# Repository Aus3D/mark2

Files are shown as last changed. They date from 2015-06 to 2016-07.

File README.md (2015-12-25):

# Aus3D Mark2 3D Printer Kit

## Overview
The Aus3D Mark2 3D Printer kit is designed to be a high-quality, easy to assemble kit-based printer. Quality and capability were the primary design goals, and the Mark2 is a printer that will not disappoint in these areas. It is based off of the [RepRap Prusa Mendel i3](http://www.reprap.org/wiki/I3) design, however the Mark2 has been redesigned from the ground up to be sturdier and more capable than traditional i3-based printers. Threaded rod and printed fasteners have been replaced with extra-thick 10mm acrylic, and the frame has been designed to to reduce vibrations - minimising excess noise and improving print quality, even during strenuous, high-frequency motions. The typical threaded-rod Z-axis has been replaced with an improved lead screw driven system, reducing Z-backlash and allowing for smoother Z motion. The rigid frame ensures all axes are held square, ensuring optimal print quality.

Full details are available on the [Aus3D wiki](http://wiki.aus3d.com.au/Mark2_Documentation).

## License
<br /><span xmlns:dct="http://purl.org/dc/terms/" property="dct:title">MK2 Printer Kit</span> by <a xmlns:cc="http://creativecommons.org/ns#" href="http://www.aus3d.com.au" property="cc:attributionName" rel="cc:attributionURL">Aus3D</a> is licensed under a <a rel="license" href="http://creativecommons.org/licenses/by-nc-sa/4.0/">Creative Commons Attribution-NonCommercial-ShareAlike 4.0 International License</a>.

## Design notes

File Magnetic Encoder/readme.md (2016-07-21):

# Magnetic Encoder Mounting Parts

The parts in this folder can be printed and used to mount magnetic encoder modules and magnetic strips to the Mark2 printer.

## X Axis
### Required Parts
* 2 x 'x-strip-bracket'
* 1 x 'x-carriage-mount'
* 2 x M3 x 15mm bolts (replace 10mm bolts in X carriage)
* 2 x M3 x 20mm bolts (for mounting strip)
* 2 x M3 nuts (for mounting strip)
* 2 x springs (for mounting strip)

Additionally, one length of wood / plastic / metal roughly 310-360mm long x 10 - 50mm wide x 1 - 5mm thick is required, and two 3mm holes must be drilled through it spaced 297mm apart. This length of material is used for mounting the magnetic strip.

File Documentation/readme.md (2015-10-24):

Assembly instructions, and other up to date documentation, can be found on the Aus3D Wiki [here](http://wiki.aus3d.com.au/Mark2_Documentation)

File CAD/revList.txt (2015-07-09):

Z rod spacing changed to 22mm
Z bracket updated to attach via 2 screws (trialled on recent kits)
frame-side-panel screwhole cutouts all changed to 3.2mm for better fit
frame-side-panel tab-cutouts all changed to 8.4 x 8.4mm for better fit

All frame t-slots designed for M3 screws and M3 nyloc nuts
All frame t-slots have filleted edges to resist over-tightening
Standard screw lengths of 12mm and 18mm

Countersunk screws for heated bed

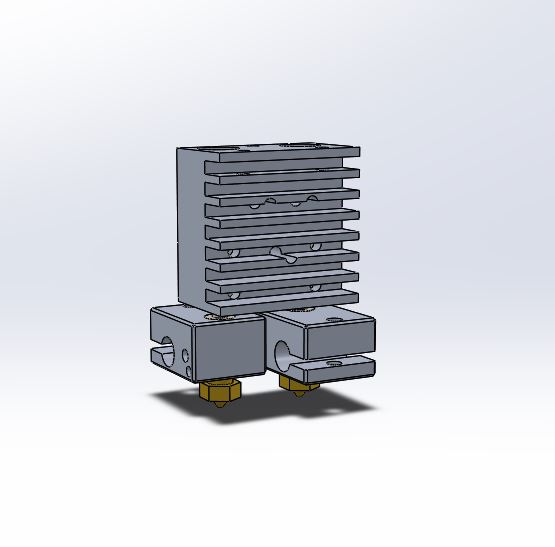
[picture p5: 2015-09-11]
CAD/Vitamins/e3d-chimera/Renderings/E3D chimera.JPG

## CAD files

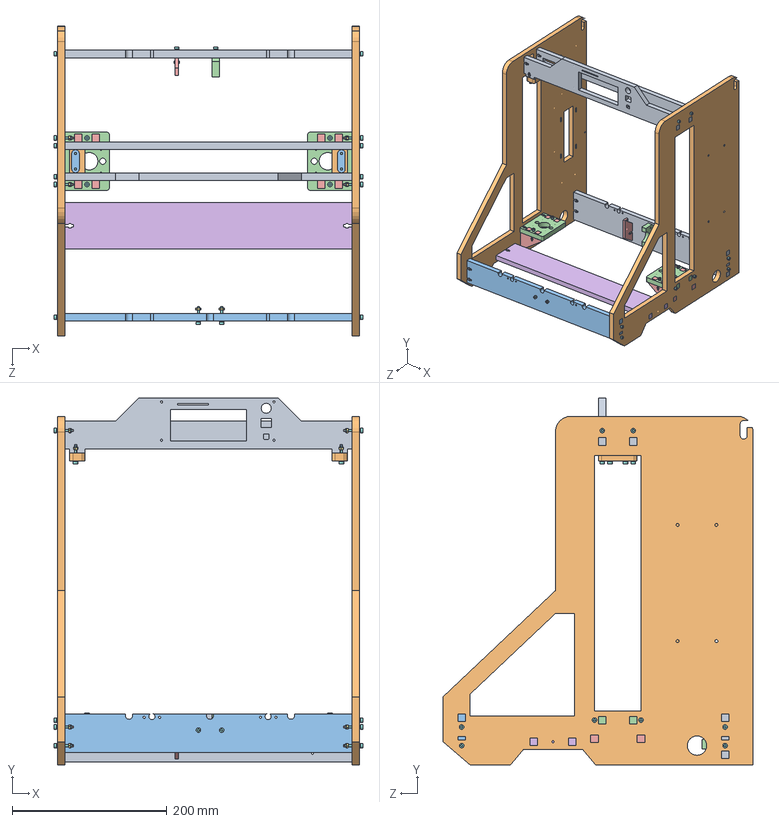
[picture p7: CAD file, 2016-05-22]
CAD/Assemblies/main-frame-assembly.SLDASM
398.4 x 473.6 x 400.0 mm
y-axis-rear
frame-side-panel x 2
y-axis-front
z-motor-bracket x 2
z-motor-brace x 4
M3-spring-washer x 32
M3-Nut x 32
M3x20-socket-head-screw x 32
frame-top-bar x 2
z-smoothrod-cap x 2
smoothrod-cap x 2
y-motor-bracket
y-endstop-holder
horizontal-brace

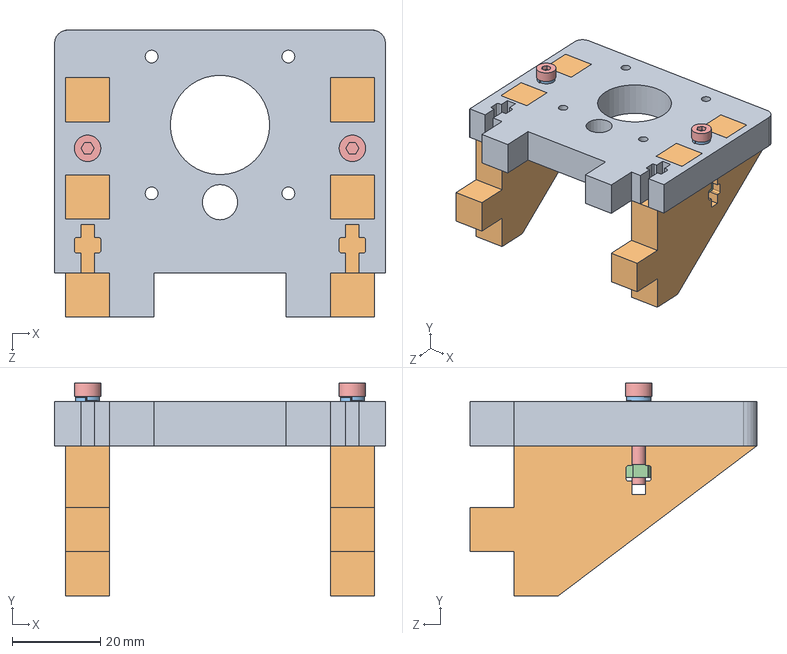
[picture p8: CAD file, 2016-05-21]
CAD/Assemblies/Z/z-motor-bracket-assembled.SLDASM
75.0 x 48.2 x 65.0 mm
z-motor-bracket
z-motor-brace x 2
M3-spring-washer x 2
M3-Nut x 2
M3x20-socket-head-screw x 2

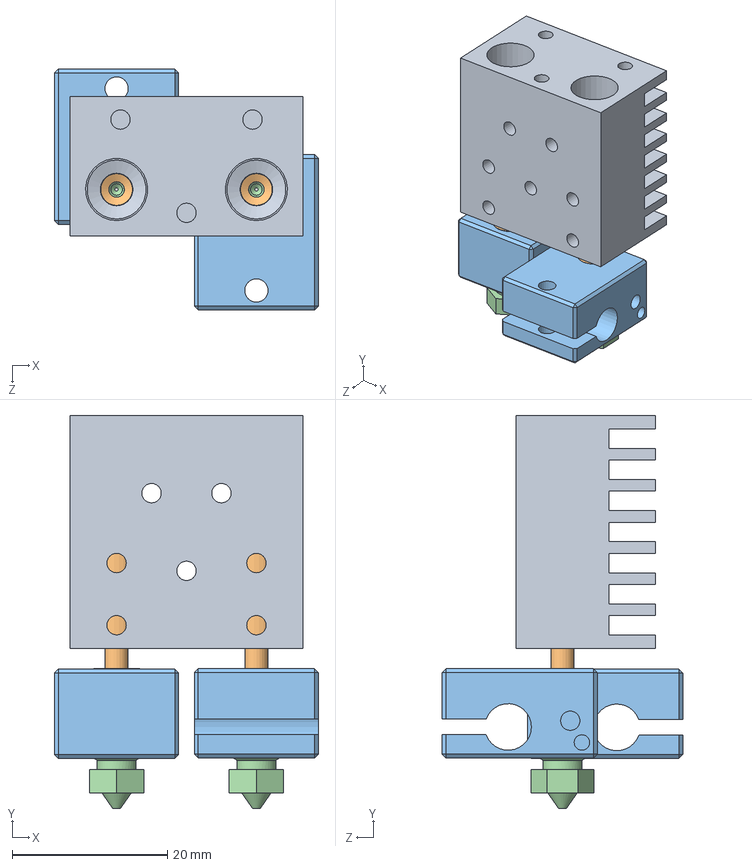
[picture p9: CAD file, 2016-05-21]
CAD/Vitamins/e3d-chimera/E3D chimera.SLDASM
34.0 x 50.6 x 31.0 mm
heat sink
heat break x 2
heater block x 2
0.4 nozzle x 2

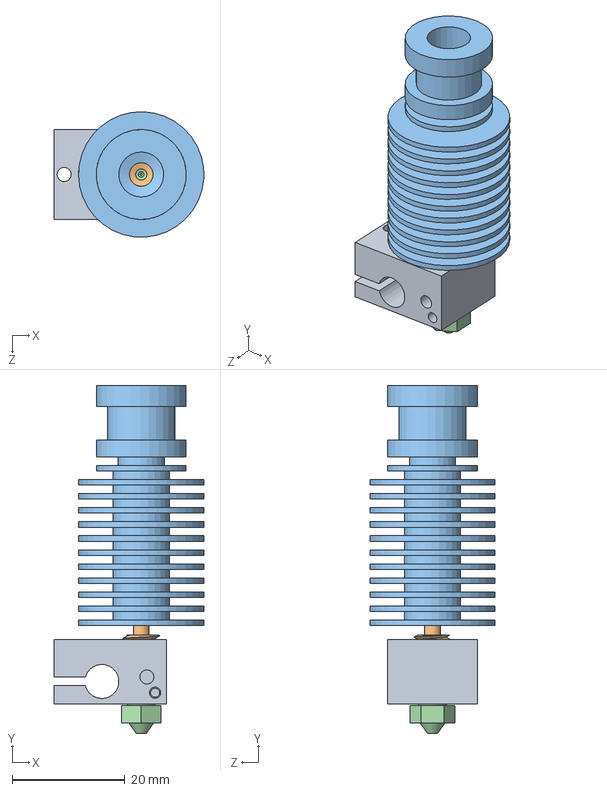
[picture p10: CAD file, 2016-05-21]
CAD/Vitamins/e3d-v6-1-75-hotend-1.snapshot.2/E3D V6 1.75 Uni model.SLDASM
26.6 x 61.9 x 22.3 mm
V6-BLOCK
V6-175-BREAK
V6-175-SINK
V6-NOZZLE-175-035

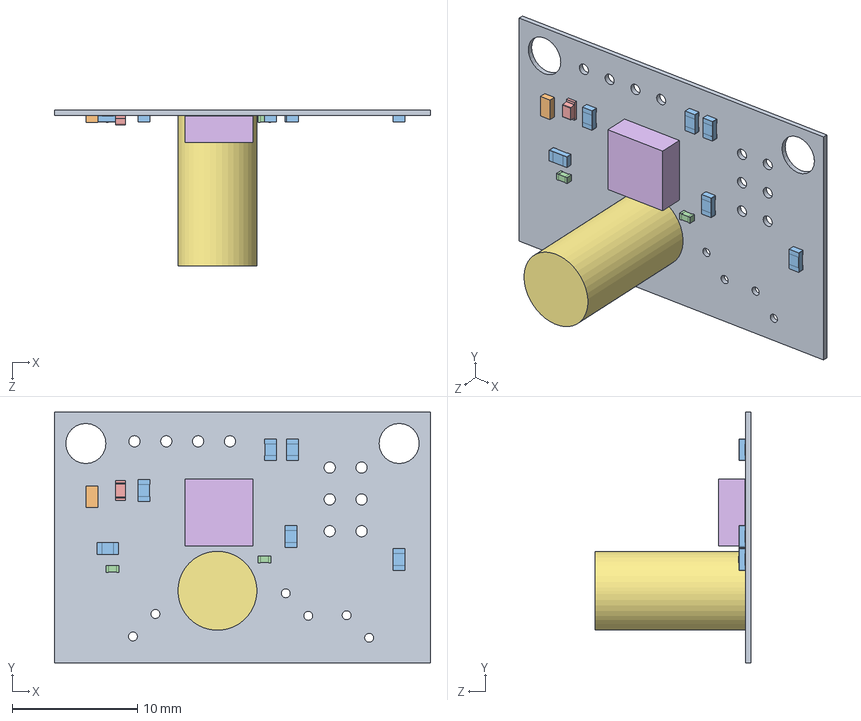
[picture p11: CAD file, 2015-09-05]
CAD/Vitamins/ZProbe/z-probe.SLDASM
30.0 x 20.0 x 12.4 mm
Board
Extruded
RES_0603_(1608_metric) x 6
CAP_0402_(1005_metric) x 2
LED_0603_APT1608_RED
Extruded_2
Part5^z-probe

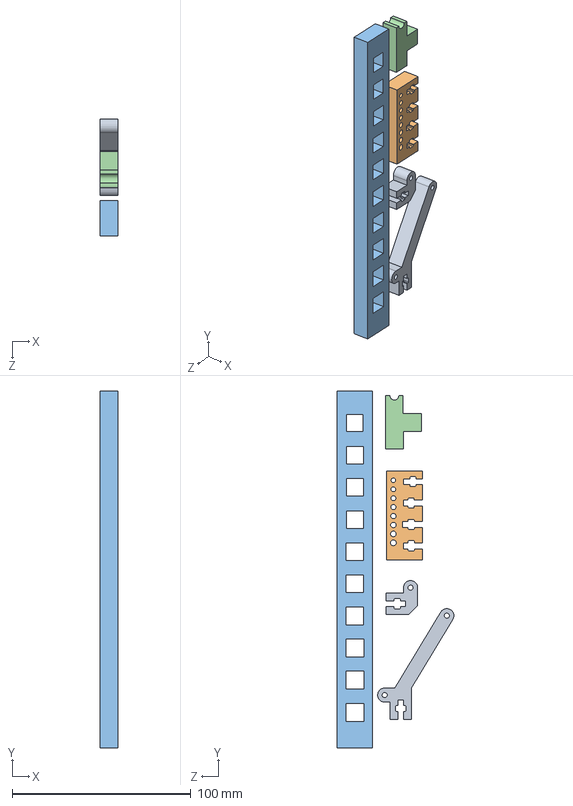
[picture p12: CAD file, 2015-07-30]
CAD/AcrylicParts/dxf/7/test10mm.SLDASM
10.0 x 200.0 x 65.5 mm
fan-mount1 x 2
calibrationPiece
calibrationPiece2
calibrationPiece3

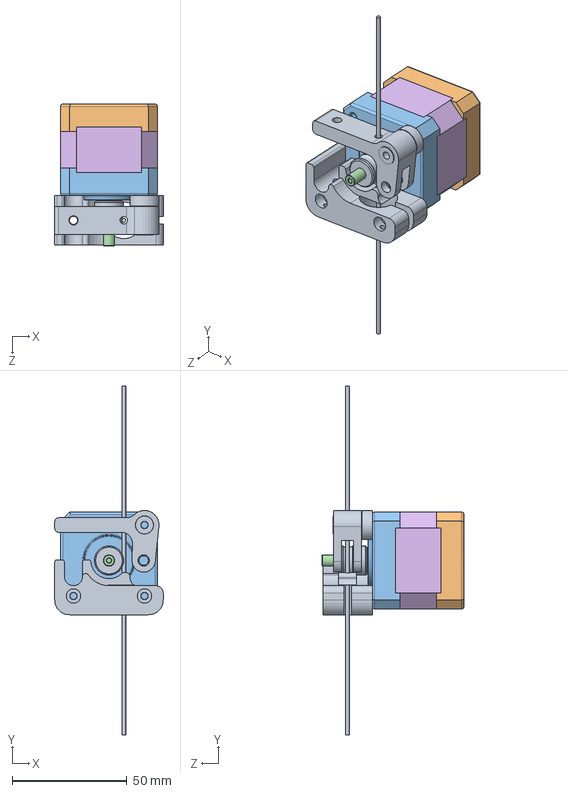
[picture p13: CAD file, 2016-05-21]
CAD/Assemblies/extruder-assembly.SLDASM
47.4 x 152.4 x 62.0 mm
alu-extruder
Base
Tapa
Eje
instrument ball bearing_68_am
core40mm

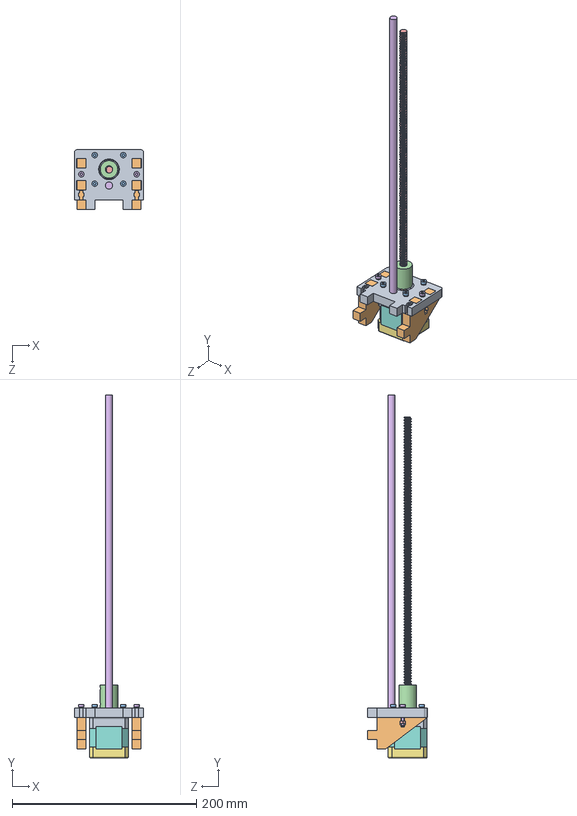
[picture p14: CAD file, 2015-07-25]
CAD/Assemblies/Z/Z-side.SLDASM
75.0 x 394.0 x 65.0 mm
z-motor-bracket
z-motor-brace x 2
M3-motor-screw x 4
M3-spring-washer x 6
M3-Nut x 2
M3x18-socket-head-screw x 2
Base
Cuerpo
Tapa
Eje
instrument ball bearing_68_am x 2
z-rod-coupler
leadscrew
smoothrod-z

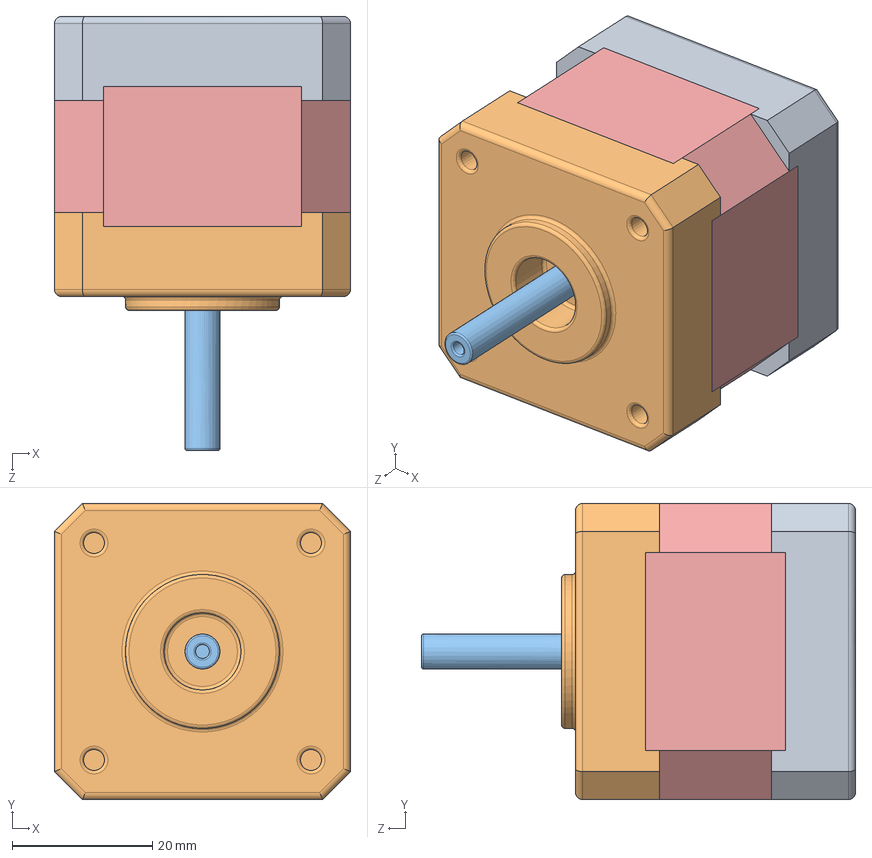
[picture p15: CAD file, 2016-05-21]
CAD/Vitamins/nema-17-stepper-motor-40mm.SLDASM
42.3 x 42.3 x 62.0 mm
Base
Tapa
Eje
instrument ball bearing_68_am
core40mm

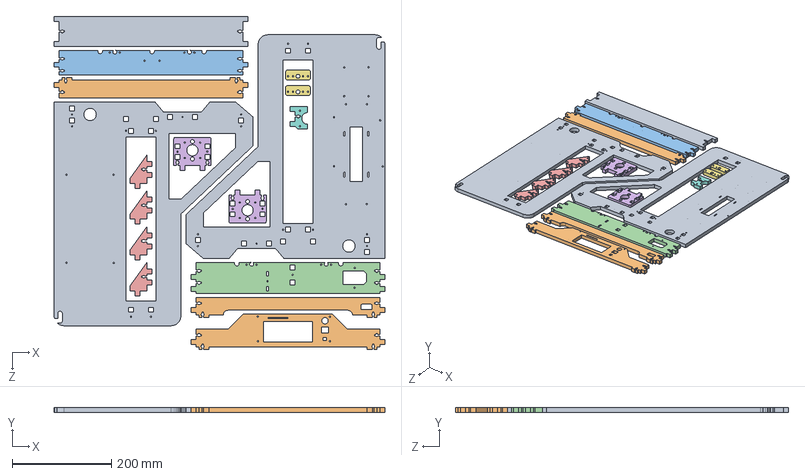
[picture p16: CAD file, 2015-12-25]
CAD/AcrylicParts/dxf/11/10mm-assem.SLDASM
665.0 x 10.0 x 669.6 mm
frame-side-panel x 2
frame-top-bar x 3
y-axis-front
y-axis-rear
z-motor-brace x 4
z-motor-bracket x 2
z-smoothrod-cap x 2
y-motor-bracket
horizontal-brace

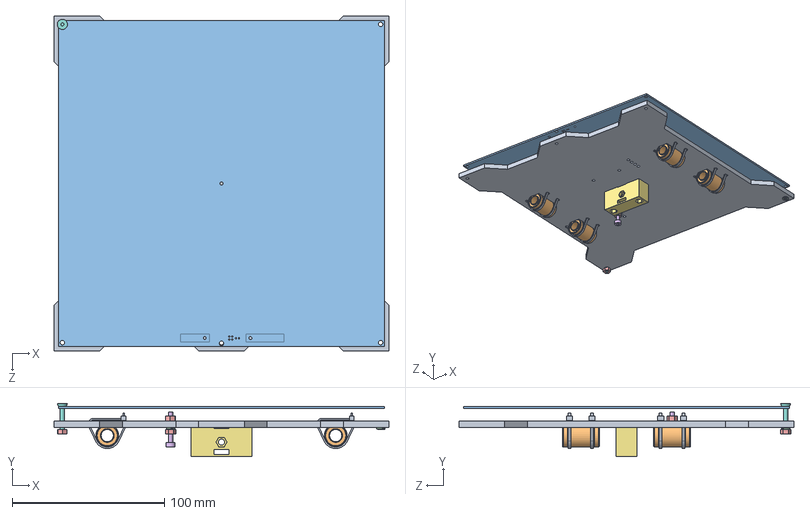
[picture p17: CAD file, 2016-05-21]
CAD/Assemblies/y-bed-assembly-basic.SLDASM
220.0 x 34.9 x 220.0 mm
y-support-plate
LM8UU x 4
M3x20-socket-head-screw
M3-Nut x 2
cableTieBed x 8
M3-spring-washer

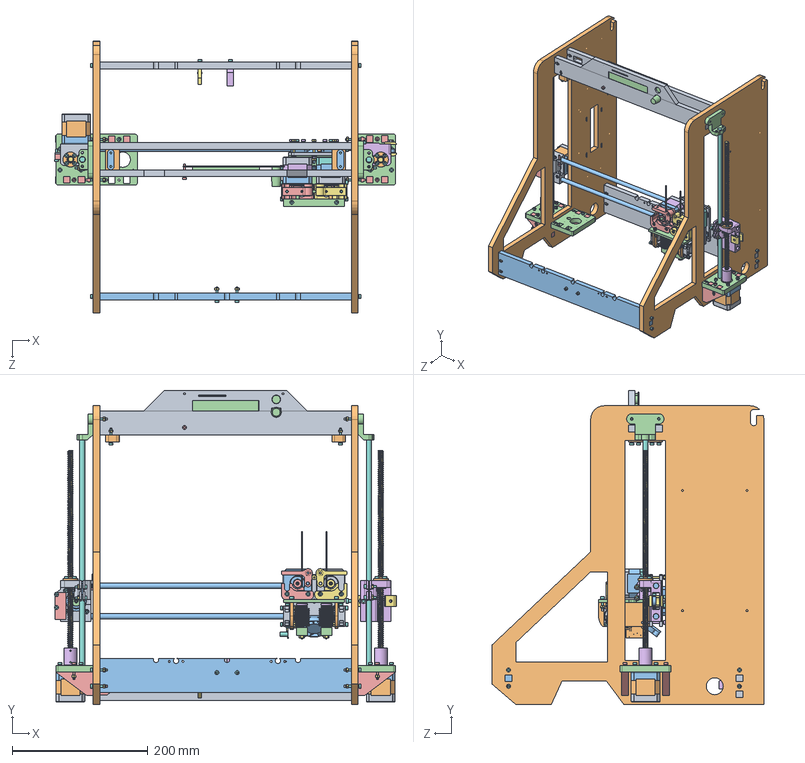
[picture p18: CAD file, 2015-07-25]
CAD/Assemblies/Z/flipped-test.SLDASM
503.5 x 462.6 x 400.0 mm
y-axis-rear
frame-side-panel x 2
y-axis-front
frame-top-bar x 2
z-smoothrod-cap x 2
smoothrod-cap x 2
M3-spring-washer x 68
M3-Nut x 57
M3x20-socket-head-screw x 45
y-motor-bracket
y-endstop-holder
z-motor-bracket x 2
z-motor-brace x 4
M3-motor-screw x 29
M3x18-socket-head-screw x 5
Base x 4
Cuerpo x 3
Tapa x 4
Eje x 4
instrument ball bearing_68_am x 9
z-rod-coupler x 2
leadscrew x 2
smoothrod-z x 2
x-motor
carraigeNut x 2
LM8UU x 6
GT2_20tooth
endstop_placeholder
x-idler
M4-Nut
M4-Bolt
624ZZ x 2
x-carriage-mount-plate-dual
alu-extruder
core40mm
Mirroralu-extruder
MirrorBase
MirrorTapa
MirrorEje
Mirrorcore40mm
V6-BLOCK x 2
V6-175-BREAK x 2
V6-175-SINK x 2
V6-NOZZLE-175-035 x 2
M3x10-socket-head-screw x 4
x-carriage-front-dual x 2
Board
Extruded
RES_0603_(1608_metric) x 6
CAP_0402_(1005_metric) x 2
LED_0603_APT1608_RED
Extruded_2
Part5^z-probe
12VDC-1.1875-X-0.375-DELTA-BOX-FAN x 2
x-carriage-brace-dual x 2
fan 40mm
x-carriage-dual-fan-brace x 2
x-carriage-tensioner x 2
M3-x-carriage-screw x 5
m3x25-countersunk-screw x 3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

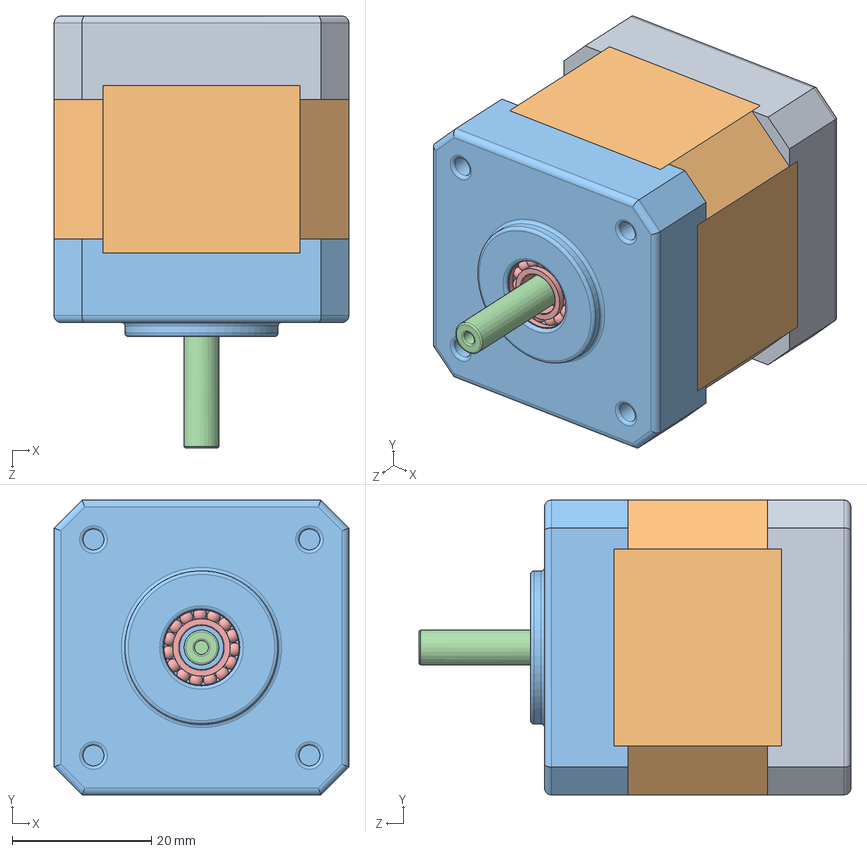
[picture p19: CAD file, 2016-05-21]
CAD/Vitamins/nema-17-stepper-motor.SLDASM
42.3 x 42.3 x 62.0 mm
Base
Cuerpo
Tapa
Eje
instrument ball bearing_68_am x 2

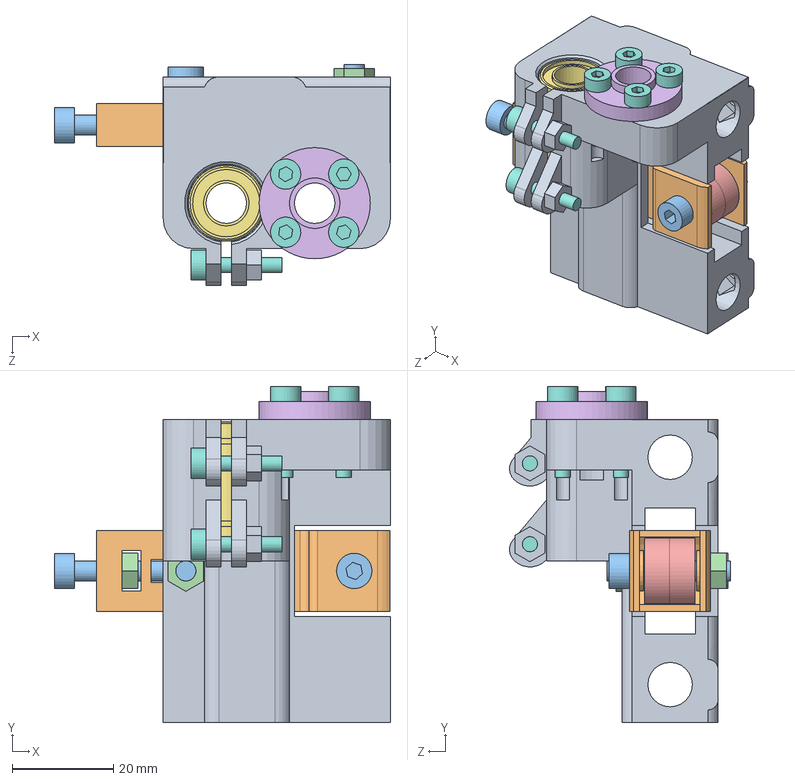
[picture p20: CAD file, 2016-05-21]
CAD/Assemblies/x-idler-assembly.SLDASM
66.5 x 66.5 x 43.7 mm
x-idler
x-idler-tensioner
M4-Bolt x 3
M4-Nut x 3
624ZZ x 2
carraigeNut
LM8UU
M3-motor-screw x 6
M3-Nut x 2

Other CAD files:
CAD/AcrylicParts/dxf/10/10mm-assem.SLDASM
CAD/Assemblies/x-carriage-acrylic.SLDASM
CAD/Vitamins/Mirrornema-17-stepper-motor-40mm.SLDASM
CAD/AcrylicParts/dxf/11/4-5mm-2-assem.SLDASM
CAD/AcrylicParts/Dual-Extruder/x-carriage-brace-dual.SLDPRT
CAD/AcrylicParts/Dual-Extruder/x-carriage-dual-fan-brace.SLDPRT
CAD/AcrylicParts/Dual-Extruder/x-carriage-front-dual.SLDPRT
CAD/AcrylicParts/Dual-Extruder/x-carriage-mount-plate-dual.SLDPRT
CAD/AcrylicParts/STLs/frame-side-panel-left.STL
CAD/AcrylicParts/STLs/frame-side-panel-right.STL
CAD/AcrylicParts/STLs/frame-top-bar-lcd.STL
CAD/AcrylicParts/STLs/frame-top-bar-rear.STL
CAD/AcrylicParts/STLs/horizontal-brace.STL
CAD/AcrylicParts/STLs/smoothrod-cap.STL
CAD/AcrylicParts/STLs/y-axis-front.STL
CAD/AcrylicParts/STLs/y-axis-rear.STL
CAD/AcrylicParts/STLs/y-endstop-holder.STL
CAD/AcrylicParts/STLs/y-motor-bracket.STL
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

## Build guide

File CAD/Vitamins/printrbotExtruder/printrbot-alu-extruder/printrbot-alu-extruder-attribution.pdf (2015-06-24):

# Printrbot Alu Extruder

## By printrbot

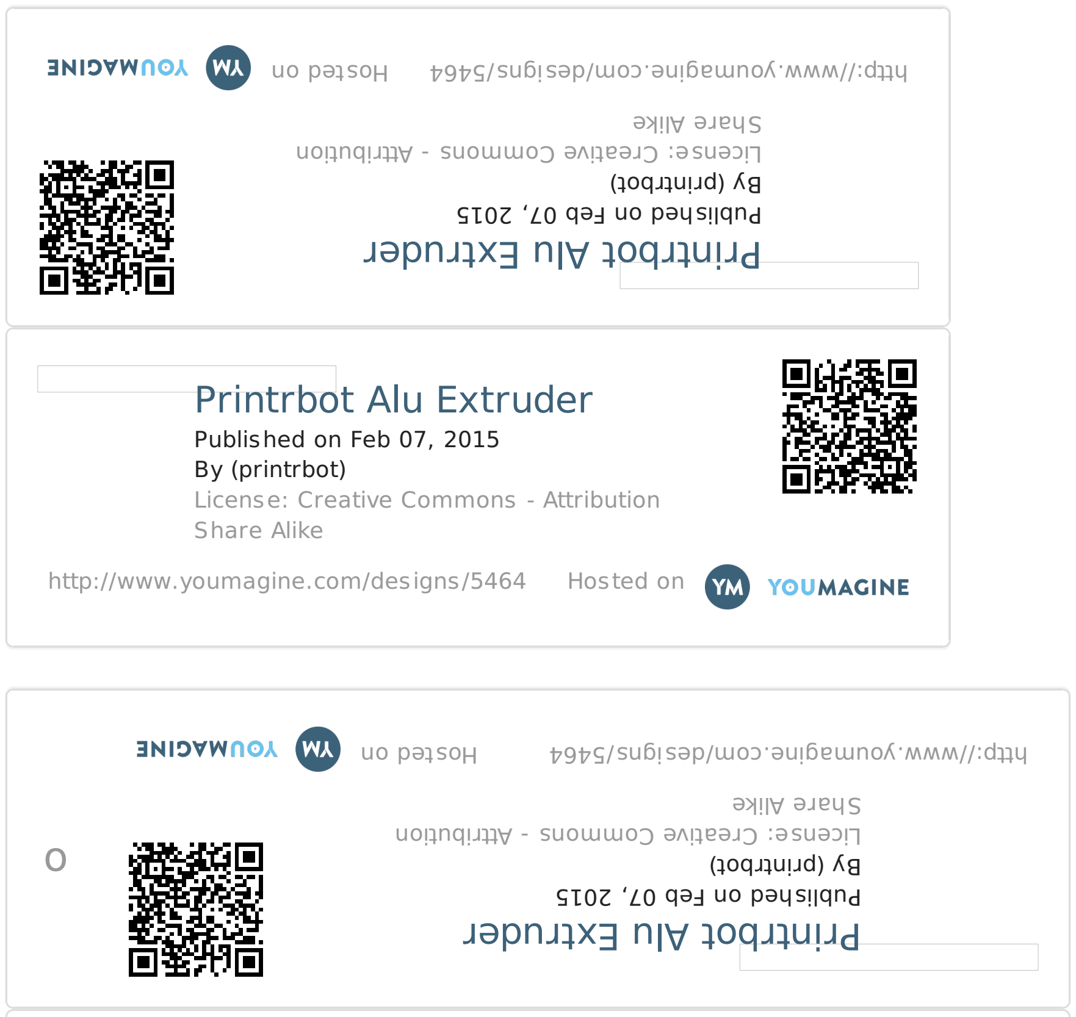
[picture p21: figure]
Printrbot Alu Extruder; Published on Feb 07, 2015 By (printrbot) License: Creative Commons - Attribution Share Alike; http://www.youmagine.com/designs/5464; Hosted on

o

## Printrbot Alu Extruder

Published on Feb 07, 2015
By (printrbot)
License: Creative Commons - Attribution Share Alike

http://www.youmagine.com/designs/5464 Hosted on

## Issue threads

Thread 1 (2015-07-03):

T-Slot Nut Trap Dimensions

Aus3D, 2015-07-03:
Need to adjust nut traps for laser kerf. Currently width is too great, nuts can spin freely making assembly difficult.

Aus3D, 2015-07-03:
Fixed.

Closed 2015-07-03.

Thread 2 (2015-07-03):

Adjust X-Carriage LM8UU Cutouts

Aus3D, 2015-07-03:
Current cutouts are spaced too large, allow carriage to rub against smoothrods. Cutouts need to be smaller to cause larger spacing between extruder front + back.

Spacing is only off by a fraction, even a 10th of a millimeter shift would correct it.

Aus3D, 2015-07-03:
Corrected.

Closed 2015-07-03.

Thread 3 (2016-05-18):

PSU Mounting Bolts

chrissbarr, 2016-05-18:
Mounting bolts for PSU need a rework. The threaded fittings that they match up with are intended for the PSU's internal electronics, not external mounting - this makes mounting the PSU difficult.

The correct holes have different placement and are M4 (I believe). Need to adjust holes in frame and add bolts to BOM to suit.

chrissbarr, 2016-05-21:
Fixed in d20f9344806e614bf6a624aec11c0c304346e3d8.

Closed 2016-05-21.

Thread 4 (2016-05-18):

Nut slots in Z brackets

chrissbarr, 2016-05-18:
The T-slot cutouts for the M3 nuts are incorrectly dimensioned in the Z bracket acrylic pieces. They are slightly over-dimensioned and can sometimes allow the nut to turn freely during assembly, making things difficult.

Check the dimensioning and update to match all other t-slot cutouts.

Closed 2016-05-21.

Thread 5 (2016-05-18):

Print Fan Mount Removability

chrissbarr, 2016-05-18:
Change the screw holes that mount the layer fan bracket to the X carriage to be open-ended slots ('U'), so that the fan bracket can be removed without completely removing the 30mm bolts holding the carriage in place.

Closed 2016-05-21.

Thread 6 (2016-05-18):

RAMPS and Pi Placement

chrissbarr, 2016-05-18:
Intended orientation of Raspberry Pi is with USB ports exiting upwards. However, due to the symmetrical nature of the Pi's mounting holes it can be installed 'upside-down', in which case the USB cables can collide with the nearby RAMPS board.

Closed 2016-05-21.

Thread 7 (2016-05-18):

Smoothieboard Mounting

chrissbarr, 2016-05-18:
Smoothieboard mounts close to rear edge of printer. This means that wiring exiting Smoothieboard overhangs the rear of the printer and is difficult to organise / tidy. Consider moving Smoothieboard forward or otherwise adjusting position to suit.

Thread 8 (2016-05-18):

Key Acrylic Tabs + Slots

chrissbarr, 2016-05-18:
Consider adjusting the sizes of the different tabs and slots in the acrylic pieces so that they cannot be installed backwards or incorrectly. Should make assembly easier and prevent mistakes.

Closed 2016-05-21.

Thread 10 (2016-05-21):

Print fan mount prone to breaking

chrissbarr, 2016-05-21:
Print fan mount requires strengthening on longest prong, direction of layer lamination + relatively small width of part means it can be easily damaged if something goes wrong.

Closed 2016-05-21.

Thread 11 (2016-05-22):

Additional Wiring Slot

chrissbarr, 2016-05-22:
Additional wiring slot on left side-panel, between both top panels, would be useful. Would allow for running wiring from X-carriage + LCD along outside of printer instead of inside. Should be supplemental to existing rear-facing wiring slot in top panels.

Closed 2016-05-22.

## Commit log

2015-06-24 Initial Commit
    Design as used in first manufacturing test.
    [624ZZ.SLDPRT, Alu_Extruder_v1.stl, Alu_Extruder_v1.stp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]
2015-07-03 Fixes
    Printed LM8UU diameter fix, work on single + dual extruder.
    [Base.SLDPRT, Cuerpo.SLDPRT, E3D V6 1.75 Uni model.SLDASM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]
2015-07-03 X Carriage LM8UU Cutout Parametric
    Updated LM8UU cutouts on acrylic X carriage to be easily adjustable.
    [x-carriage-front.SLDPRT]
2015-07-03 X Carriage LM8UU Spacing
    Adjusted cutout size to space front and back plates slightly further
    apart. Should prevent any chance of acrylic pieces rubbing on
    smoothrods. Also allows for slightly longer screws to be used.
    [x-carriage-acrylic.SLDASM, x-carriage-front-dual2.SLDPRT, x-carriage-front.SLDPRT]
2015-07-03 Adjust M3 Holes
    Shrink holes slightly. Current fit is very good, but there is room to
    tighten the holes slightly.
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2015-07-08 Overhaul
    Bed lowered, printed bearing blocks removed. Y Endstop moved to inside
    frame, decreasing footprint. X-carriage / extruder rework, added Z
    probe.
    [12VDC-1.1875-X-0.375-DELTA-BOX-FAN.SLDPRT, Mirrorextruder-assembly1.SLDASM, Mirrornema-17-stepper-motor-40mm.SLDASM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]
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2015-07-09 New X Tensioner
    Changed X axis design. X idler is now fixed in place, belt tensioner is
    inside x carriage. This fixes the idler wobbling / vibrating / rotating
    slightly, and is more compact.
    [M3x10-socket-head-screw.SLDPRT, M3x18-socket-head-screw-and-spring-washer.SLDASM, M3x18-socket-head-screw.SLDPRT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]
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2015-07-11 Extruder Rework
    Initial tests show E3D hotend will not fit fully inside PB extruder.
    Updated X carriage to have groove mount for hotend. Added belt-clip for
    non-tensioner side of carriage.
    [614540344.sldasm, 630747112.sldasm, C2.sldasm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]
2015-07-11 Belt Clip Adjustment
    Deepened hole on X belt clip.
    [x-carriage-tensioner-clip.SLDPRT]
2015-07-11 LCD Frame Part
    Added top-bar part for LCD smart controller. Modified rear top-bar to
    have cable cutout.
    [LCDsmartControllerPlaceholder.SLDPRT, frame-side-panel.SLDPRT, frame-top-bar.SLDPRT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]
2015-07-11 Raspberry Pi Mounting
    Added holes to mount Raspberry Pi 2 / B+ / A+
    [frame-side-panel.SLDPRT, main-frame-assembly.SLDASM]
2015-07-11 Changed Wiring Slot
    Shrunk wiring slot to be less noticeable, more behind RAMPS board.
    [frame-side-panel.SLDPRT]
2015-07-11 Begin Dual Extruder Rework
    [M3x10-socket-head-screw.SLDPRT, Mirroralu-extruder.SLDPRT, Mirrorextruder-assembly1.SLDASM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]
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2015-07-12 Dual Extruder Overhaul
    Significantly reworked dual extruder setup. Dual extruder now gets 180mm
    on the X axis.
    [614540344.sldasm, 630747112.sldasm, C2.sldasm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]
2015-07-12 Tweaks
    Tweaks to extruder (I don't remember). Updated Y bed support plate to
    have slots instead of M3 holes - will still suit M3 screws for printed
    parts, otherwise better chance of fitting cable ties.
    [M3-x-carriage-screw.SLDPRT, M3x18-socket-head-screw-and-spring-washer.SLDASM, M3x20-socket-head-screw-and-spring-washer.SLDASM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]
2015-07-12 Prototype Unit 2
    Let's try this again! First unit was 110% awesome - this time we're
    aiming for 120%.
    [10mm-1.dxf, 4-5mm-1.dxf, 4-5mm-2.dxf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]
2015-07-14 Added Fan Control Board
    Added temperature-based fan control board. Tidied directories.
    [AFC.PrjPCB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]
2015-07-16 Prototype 2 New Drawings
    Initial drawings had a problem with line segments. Revised drawings.
    [10mm-1.dxf, 10mm-assem.DXF, 10mm-assem.SLDASM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]
2015-07-17 Fan Expansion, Z Probe Rework
    Many reworkings of Z probe board. Fixed IR LED polarity. More space for
    connector. Larger inductor size. New fan expansion board, 4 x 12V fan
    mosfets, 2 x temp controlled, 2 x firmware controlled..
    [AFC1.PcbDoc, ExtruderZProbe.PrjPcb, PCB1.PcbDoc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]
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2015-07-23 Updated Y Idler
    Updated to remove need for M4 washers, added inset for M3 nuts to assist
    in assembly. Adjusted to suit M4x20mm screw, as with X Idler.
    [x-idler.SLDPRT, y-idler.SLDPRT]
2015-07-25 Fan Expansion Board V2
    Tests with V1 seem to be working correctly. Sent V2 to PCB fab.
    [AFC1.PcbDoc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]
2015-07-25 Reworking Tolerances
    Reworking acrylic tolerances and kerfs.
    [10mm-assem.SLDASM, 4-5mm-3-assem.SLDASM, M3-motor-screw.SLDPRT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]
2015-07-27 Move R1 R2
    R1 and R2 collide with JST plug. Shifted slightly to avoid problems.
    [PCB3.PcbDoc]
2015-07-29 Increase Fan Cutout
    Increased size of hotend fan cutout on extruder carriage. Current size
    is slightly smaller than fan's effective diameter, causing some air to
    bounce back and whistle.
    [main-frame-assembly.SLDASM, x-carriage-brace.SLDPRT, x-idler-assembly.SLDASM]
2015-07-30 Tweaks
    Added rod-tighteners to X idler to allow easier installation of X/Z
    axis. Test pieces for acrylic tolerances created.
    [10mm.DXF, 4-5mm-3-assem.SLDASM, 4-5mm-3-assem.SLDDRW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]
2015-08-01 X Axis Update
    Updated X Idler to slide along X smooth rods until bolts are tightened.
    Allows for easier alignment with Z axis during assembly.
    [AFC1.PcbDoc, x-idler.SLDPRT, x-motor.SLDPRT]
2015-08-01 Three-Hole Mounting Fix
    Previous arrangement had cables exiting front of printer. Changed so
    cables exit to rear.
    [y-support-plate.SLDPRT]
2015-08-06 Updated Fan Duct
    Updated fan duct to better fit fan.
    [x-carriage-blower-fan-duct.SLDPRT]
2015-08-06 Spool Holder Update
    Tweaked rod adaptor to print better.
    [spool-holder-rod-adaptor.SLDPRT]
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2015-08-09 TinyFan
    Added a tiny fan expansion board for RAMPS.
    [Board.sldprt, D1.sldasm, D2.sldasm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]
2015-08-15 Tidying
    Tidied up, removed old components no longer in use for clarity. Added
    bill of materials to documentation for beta kits.
    [10mm-assem.DXF, 10mm-assem.SLDASM, 10mm-assem.SLDDRW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]
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2015-09-04 Bed Plate Fix
    Noticed issue where bed plate can collide with smoothrod-caps if things
    are pushed around a bit. Making bed support-plate sit slightly higher on
    bearings to mitigate chances of this happening.
    [y-support-plate.SLDPRT]
2015-09-05 New Fan Duct
    Added new fan duct for blower fan. Improved on old design to no longer
    blow air over hotend heater block. Quick test shows fan can now run 100%
    without overpowering hotend heater cartridge.
    [614540344.sldasm, 630747112.sldasm, C2.sldasm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]
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2015-09-18 Added Filament Cutout
    Added cutout in top bar to make it easier for filament to reach extruder
    when approaching 200mm print height
    [M3x18-socket-head-screw-and-spring-washer.SLDASM, frame-side-panel.SLDPRT, frame-top-bar.SLDPRT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]
2015-09-18 Tidying X Carriage
    Moving order of spacers/washers, tidying assembly.
    [frame-side-panel.SLDPRT, main-frame-assembly.SLDASM, x-carriage-acrylic.SLDASM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]
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2015-09-19 Massive Overhaul
    Many tiny changes. Tweaked a lot of screw hole positions, shifted
    tabs/slots around slightly, added cable management + endstop trigger to
    single-carriage. Adjusted mounting holes for RAMPS / Smoothieboard /
    Melzi for better cable / axis clearance. Increased maximum possible X
    travel slightly. Increased maximum possible Z travel slightly. Must...
    have... every... millimetre.
    So yeah, compatibility with earlier prototypes is probably pretty
    broken. No game-changing modifications, just lots of little tweaks.
    [M3-motor-screw.SLDPRT, M3-x-carriage-screw.SLDPRT, M3x10-socket-head-screw.SLDPRT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]
2015-09-24 Ongoing Tweaks
    Still tweaking things. I don't remember all the changes, just general
    tweaks to make assembly easier.
    [E3D V6 1.75 Uni model.SLDASM, G3D_Mech_Endstop.SLDPRT, M3-motor-screw.SLDPRT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]
2015-09-24 Update X Motor Part
    Rod tightening screws now enter from the back, same as the X Idler part
    in order to prevent accidentally skewing the rods during tightening.
    Added cutout for 8mm smooth rod to Z-bracket to work in extended axis
    configuration, X printed parts no longer need to be reversed.
    [M3-motor-screw.SLDPRT, M3x10-socket-head-screw.SLDPRT, M3x20-socket-head-screw.SLDPRT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]
2015-09-24 Dual Extruder Tweaks
    Dual extruder redesign four-thousand and sixty-seven.
    *cries*
    But hey, it's pretty awesome. Keeps getting awesomer. I need to stop
    tweaking.
    [M3-x-carriage-screw.SLDPRT, M3x18-socket-head-screw-and-spring-washer.SLDASM, M3x18-socket-head-screw.SLDPRT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]
2015-10-12 IEC Panel Socket
    Added cutout + screw holes for IEC Panel Socket on rear of frame.
    [E3D V6 1.75 Uni model.SLDASM, IECpanel.SLDPRT, Inlet Module Plug Fuse Switch Male Power Socket 10A 250V 3 Pin IEC320 C14.SLDPRT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]
2015-10-16 Tweaking
    Increase cutout for bed tightening screws on front and back panels
    slightly. Changed orientation of heated bed in 3-point mounting. Various
    other small improvements.
    [M3-motor-screw.SLDPRT, M3-x-carriage-screw.SLDPRT, M3x10-socket-head-screw.SLDPRT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]
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2015-10-16 Bed Cable Ties
    Modelled and added cable ties that hold the Y-axis bearings in place.
    [cableTieBed.sldprt, x-carriage-acrylic-dual2.SLDASM, x-motor-assembly.SLDASM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]
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2015-10-31 Fixing Compile Errors
    Relocate Z Probe model to Vitamins folder. Updated files to SW2016.
    [0.4 nozzle.SLDPRT, 12VDC-1.1875-X-0.375-DELTA-BOX-FAN.SLDPRT, 624ZZ.SLDPRT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]
2015-11-18 Reinforced Frame
    Added additional structural member to prevent frame from twisting (XY
    axis becoming non-perpendicular). Not really a big problem, can only
    really happen if frame is lifted or moved when in use. This should fix
    it though.
    Also adjusted X and Y idlers to suit F624ZZ bearings to keep belt
    centred correctly.
    [IECpanel.SLDPRT, PSU.SLDPRT, frame-side-panel.SLDPRT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]
2015-11-22 Belt Screw Cap
    Added printed part to spread tension from screw in y-tensioner across
    area of belt. Prevents screw from tearing belt during tightening.
    [belt-screw-cap.SLDPRT, belt-screw-cap.STL]
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2015-11-28 Assembly Tweaks
    Added in final bolts, washers etc. Tidying and checking BOM.
    [10mm-assem.SLDASM, 10mm-assem.SLDDRW, 10mm.DXF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]
2015-12-04 Production Model
    Adjusted new horizontal brace, optimised part layouts for laser cutting, minor tweaks to printed parts. Adjusted assemblies to check BOM etc.
    [10mm-assem.SLDASM, 10mm-assem.SLDDRW, 10mm.DXF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]
2015-12-11 Y Belt Clamp Fix
    Increase size of screw holes connecting part to bed support plate from 3.2mm to 3.5mm to make installation easier.
    [y-belt-clamp.SLDPRT, y-belt-clamp.STL]
2015-12-11 Update Spool Adaptors
    Modified spool rod adaptors to be more easily printable.
    [spool-holder-rod-adaptor-printable.STL, spool-holder-rod-adaptor.SLDPRT]
2015-12-12 Flexible Filament
    Slight modification to E3D HotEnd cap printed part to allow PTFE to pass further inside extruder. Should further improve handling of flexible materials.
    [E3D-cap.SLDPRT]
2015-12-12 E3D Cap Improvement
    Increase ease of assembly by providing channel for extruder motor bolt to pass through. Previously part could interfere with bolt, which made tightening bolt difficult.
    [E3D-cap.SLDPRT, E3D-cap.STL]
2015-12-12 E3D Volcano Adaptor
    E3D volcano add-ons lower the HotEnd nozzle by 10mm, which prevents the IR probe from functioning. This bracket lowers the IR probe to suit.
    [e3d-volcano-adaptor.SLDPRT, e3d-volcano-adaptor.STL]
2015-12-13 Printing Tweaks
    Minor tweaks of printed parts to improve printability. Fixed issue where X idler tensioner had section too thin to successfully slice (led to excessive stringing). Adjusted location and size of bolt channel on E3D cap. Increased size of bolt hole on belt screw cap.
    [E3D-cap.SLDPRT, E3D-cap.STL, belt-screw-cap.SLDPRT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]
2015-12-16 Loose Nut Fixed
    Fixed problem where t-slots for nuts securing top bars to side panels were slightly too large, leading to the nut spinning freely and difficulty during assembly.
    [frame-top-bar.SLDPRT]
2015-12-16 Wiring Slot
    Slightly increased size of wiring slot behind RAMPS from 25x110mm to 30x115mm to make it easier to tuck wiring away.
    [frame-side-panel.SLDPRT]
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2015-12-23 Remove Old Documentation
    All documentation is available and updated at http://wiki.aus3d.com.au/Mark2_Documentation. Old documentation in repository was out of date and potentially confusing, removing for tidiness.
    [bom.xlsx]
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2015-12-25 Fan Mount Improved
    Improved printability of fan mount, support material is no longer required.
    [x-carriage-blower-fan-mount.SLDPRT, x-carriage-blower-fan-mount.STL]
2015-12-25 E3D Circlip
    Added circlip intended to replace previous 'E3D Cap' file. Easier to install, fixes HotEnd in place just as sturdily, and faster to print.
    [e3d-circlip.SLDPRT, e3d-circlip.STL]
2015-12-25 X Endstop Mounting
    Modified X Motor printed part to make mounting endstop easier. Only two spacers are required (four previously) and bolts should no longer protrude to contact belt.
    [x-motor.SLDPRT, x-motor.STL]
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2016-05-21 Frame STL files
    Adding STL files of all frame parts. Hopefully they will allow easier tracking of future changes using GitHub's STL previewer.
    [frame-side-panel-left.STL, frame-side-panel-right.STL, frame-top-bar-lcd.STL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]
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2016-05-21 Z bracket nut traps fix
    Closes #4
    [z-motor-bracket.SLDPRT, z-motor-bracket.STL]
2016-05-21 Improve fan mount
    Improve print fan mount, strengthened the longer prong that could occasionally break, made part (un)installable without removing bolts entirely.
    Fixes #5 and fixes #10.
    [x-carriage-blower-fan-mount.SLDPRT, x-carriage-blower-fan-mount.STL]
2016-05-21 Control board placement
    Shifted RAMPS + other control boards down 5mm, Pi up 10mm - should improve wiring clearance between both boards when Pi is mounted with connectors exiting downwards.
    Fixes #6
    [frame-side-panel-left.STL, frame-side-panel.SLDPRT]
2016-05-21 Keying Frame
    Keying tabs / slots between acrylic parts, should make assembly more straightforward and make it harder for things to go wrong. Closes #8.
    [E3D V6 1.75 Uni model.SLDASM, E3D chimera.SLDASM, M3-motor-screw.SLDPRT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]
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2016-06-01 Improve fan duct mounting
    Fan duct now attaches to fan more securely.
    [x-carriage-blower-fan-duct2.STL, x-carriage-blower-fan-duct2.sldprt]
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2016-07-22 Fix no-extrusion setting
